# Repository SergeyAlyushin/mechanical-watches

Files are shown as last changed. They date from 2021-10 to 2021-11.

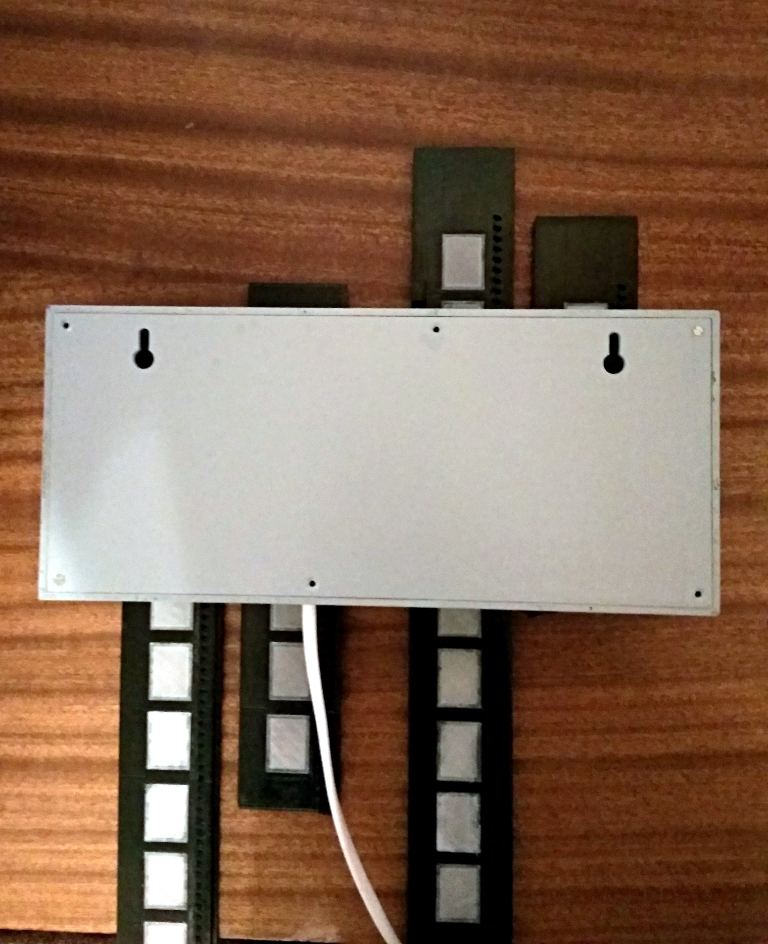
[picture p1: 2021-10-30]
IMG_5.jpg

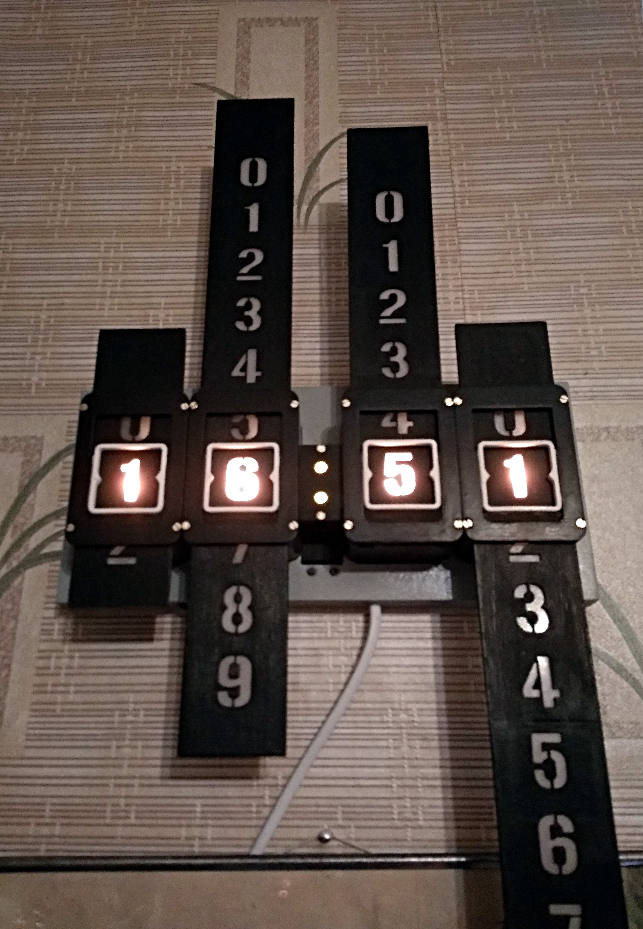
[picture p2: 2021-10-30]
IMG_6.jpg

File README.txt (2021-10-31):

Часы с шаговыми двигателями на Arduino, автор Луук Эссельбрюгге из Нидерландов, напечатанные на 3D-принтере.
Это мой вариант, немного переработанный.
------------------------------------------------------------------------- 

Компоненты:
4 микросхемы SMD 74HC595
4 микросхемы SMD ULN2003  
4 светодиода WS2812B 
1 плата Arduino Nano
1 модуль GPS NEO 6M (покупайте с большой антенной, иначе будете бегать по квартире в поисках спутника)
4 шаговых двигателя 28BYJ-48 на 5V без драйверов
4 резистора SMD 1kOm
2 резистора 0,125Вт 1кОм
1 резистор 0,125Вт 330 Ом
2 светодиода для точек, любого типа, по цвету совпадающие с подсветкой
3 тактовых кнопки DIP
4 концевых выключателя MK7
1 микровыключатель питания
4 разъема ХН2.54 на 5 контактов (папа)
4 разъема ХН2.54 на 4 контакта (папа + мама)
4 разъема ХН2.54 на 3 контакта (папа + мама)
4 разъема ХН2.54 на 2 контакта (папа + мама)
1 блок питания на 5V 3А
16 шурупов 2х10 с полукруглой головкой (для крепления мотора и платы)
24 шурупа 2х10 с головкой в потай (для крепления передних и задних крышек)
12 шурупов 1,8х5 (для крепления модулей)
8 шайб 2х5 (для крепления моторов)
---------------------------------------------------------------------------

Все детали корпуса напечатанны пластиком ABS (его легче склеивать) на 3Д принтере. Четыре корпуса Body 1-4 и корпус Body point печатались с применением поддержек.Файлы STL лежат в папке "Models"
 
4 корпуса (Body_1, Body_2, Body_3, Body_4)
4 крышки корпуса (Bracket)
4 рамки крышки корпуса (Ramka_Bracket)
1 корпус точек (Body_Point)
1 крышка корпуса точек (Lid_Body_point)
1 светофильтр крышки корпуса точек (Filter_point), печать пластиком SBS  
3 пластины (Plate1) 
2 пластины (Plate2)
1 пластина (Plate3)
1 пластина (Plate4)
3 пластинчатых соединителя (Plate_connector)
29 светофильтров пластин (Window), печать пластиком SBS 
4 шестерни шаговых моторов (Gear)
1 половина основания (Top_base_left)
1 половина основания (Top_base_Right)
1 половина задней панели основания (Bottom_base_left)
1 половина задней панели основания (Bottom_base_Right)
1 пластина соединителя задней панели (Pad_Bottom base)
1 крепление антенны GPS (Antenna)
1 крепление модуля GPS (Module GPS)
1 крепление платы Arduino (Arduino)
1 крепление тактовых кнопок (Buttoms)
----------------------------------------------------------------------------
Печатные платы драйверов изготовлены из стеклотекстолита толщиной 1мм, толще не влезут в корпус. Макет платы нарисован в программе Sprint Layout версии 6.0 и лежит в папке "Printed circuit boards".
Принципиальная схема часов лежит в папке "Image".
----------------------------------------------------------------------------
Скетч лежит в папке "ArduinoCode" и полностью работоспособен.
У автора были некоторые неточности, поэтому я внес исправления и позволю себе дать некоторые пояснения для новичков.
В версии Arduino 1.8.1 компиляция проходит без проблем.
-----------------------------------------------------------------------------
Перед загрузкой скетча, проверить, что все ниже перечисленные библиотеки у вас добавлены (они должны быть красного цвета): 
#include <FastLED.h>
#include <SoftwareSerial.h> 
#include <OneWire.h> 
#include <DallasTemperature.h>
Если библиотека черного цвета, то необходимо ее добавить в среду Arduino
-----------------------------------------------------------------------------
В комментариях ниже перечисленных строк:  
int SER_Pin = 12;   //pin 14 on the 75HC595
int RCLK_Pin = 11;  //pin 12 on the 75HC595
int SRCLK_Pin = 10; //pin 11 on the 75HC595
не правильно указана серия микросхемы, правильно - 74НС595
-----------------------------------------------------------------------------
В комментариях строки: 
int RX_GPS = 5; //RX pin on GPS module
не правильно указан контакт подключения модуля GPS, правильно подключать к контакту ТХ.
-----------------------------------------------------------------------------
При необходимости, можно изменить цвет подсветки.
Для дневного режима в строке:
int NightColor[] = {48, 255, 0};
можно поиграться со значениями {48-красный, 255-зеленый, 0-синий}
Для ночного режима в строке:
int DayColor[] = {255, 255, 255};
(этот режим я не использовал, поэтому контакт Arduino А5  я подтянул к GND через резистор 10кОм.)
-----------------------------------------------------------------------------
В зависимости от региона Вашего проживания, возможно будет необходимо подправить значение в строке:
timezoneOffset = 2;
Цифра 2 означает, что к текущему времени GPS будет прибавлено 2 часа.

Для активизации коррекции, вам необходимо нажав и удерживая кнопку "Mode" включить питание часов. Отпустить кнопку только после окончания калибровки.

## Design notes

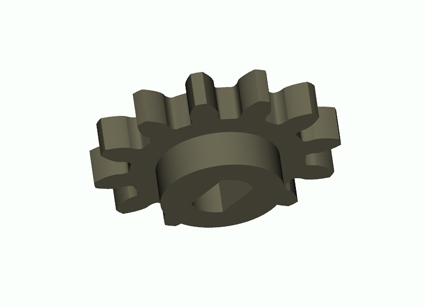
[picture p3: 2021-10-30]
Gear.jpg

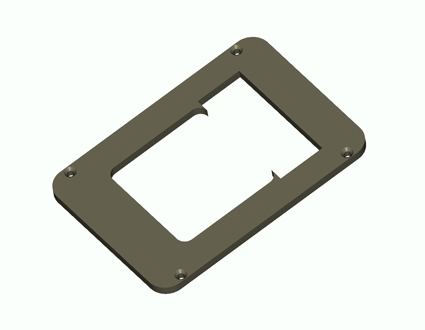
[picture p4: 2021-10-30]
Bracket.jpg

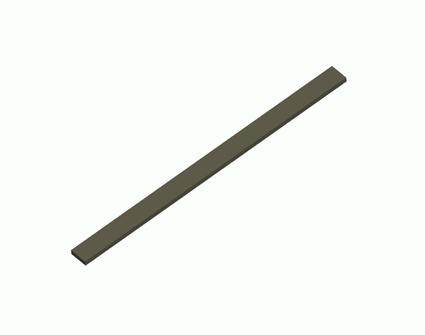
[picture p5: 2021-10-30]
Pad Botton base.jpg

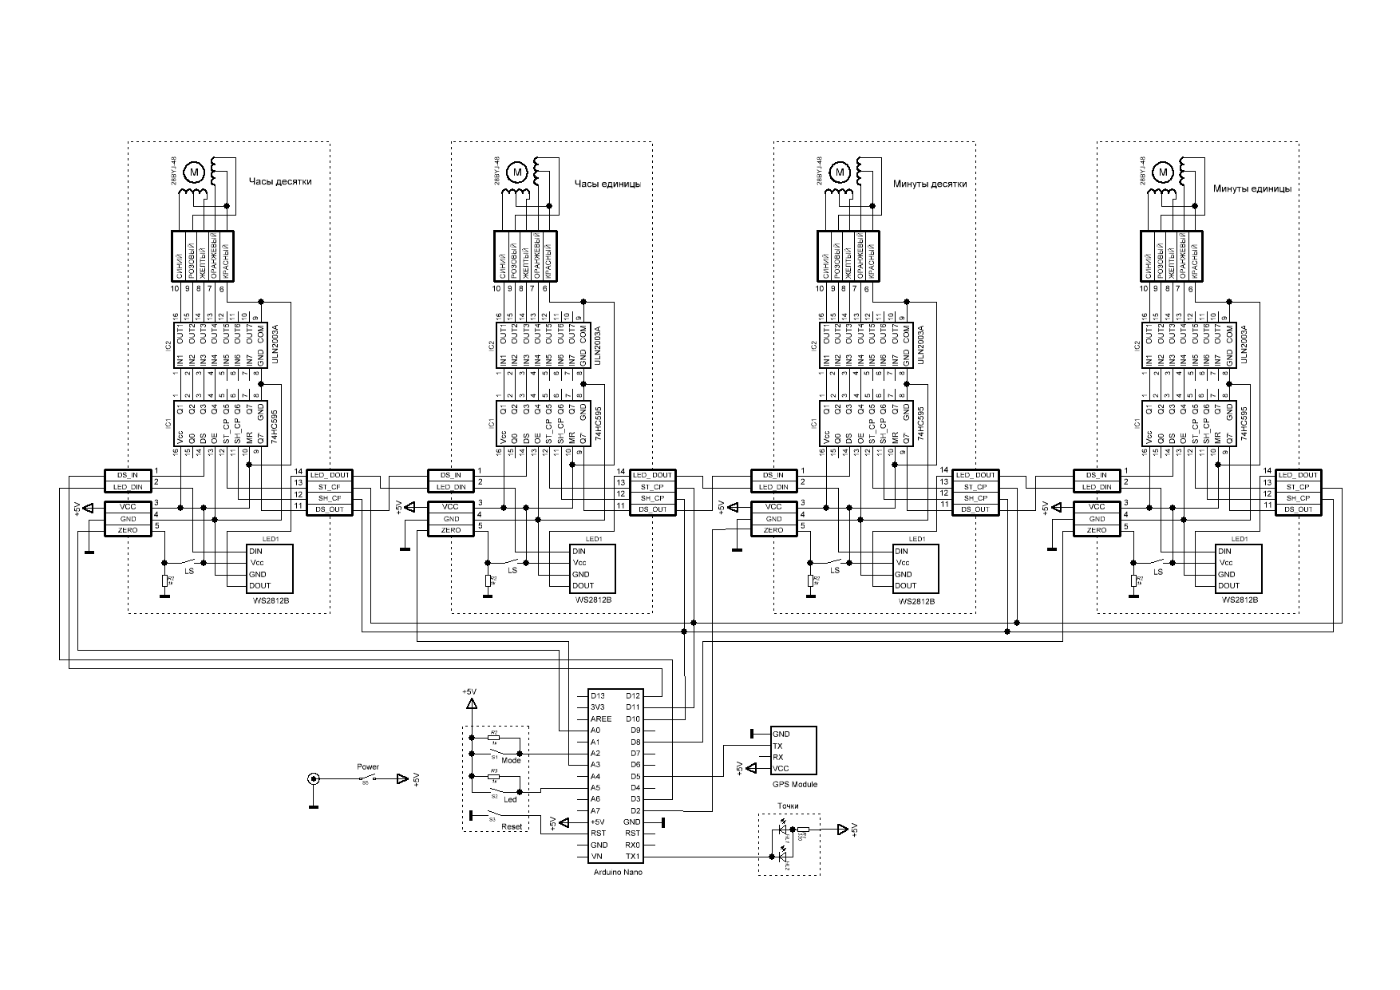
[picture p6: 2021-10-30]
Схема.GIF

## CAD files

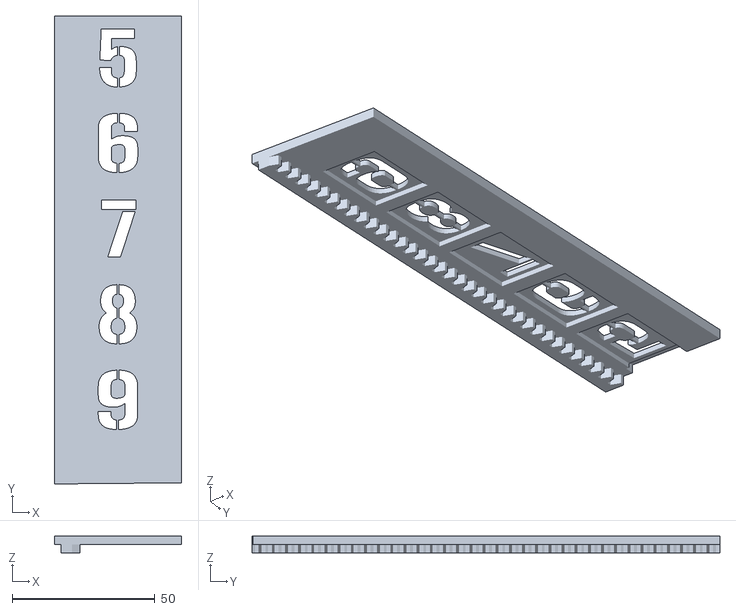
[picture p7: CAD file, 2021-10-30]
Plate2.stl
44.5 x 164.0 x 5.95

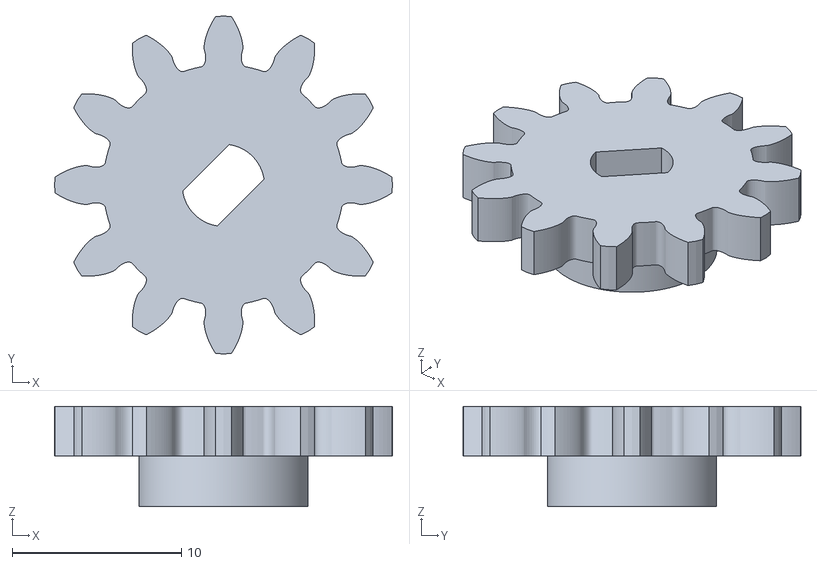
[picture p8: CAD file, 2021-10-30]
Gear.stl
20.0 x 20.0 x 5.93

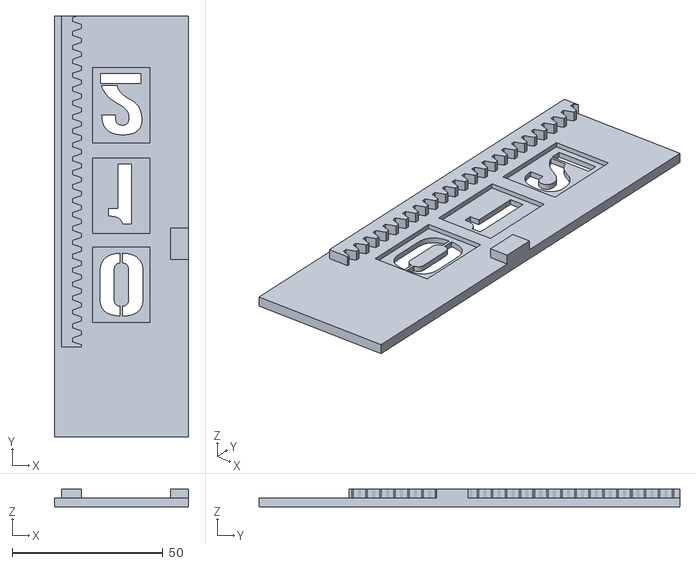
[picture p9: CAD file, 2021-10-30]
Plate3.STL
44.5 x 139.5 x 5.95

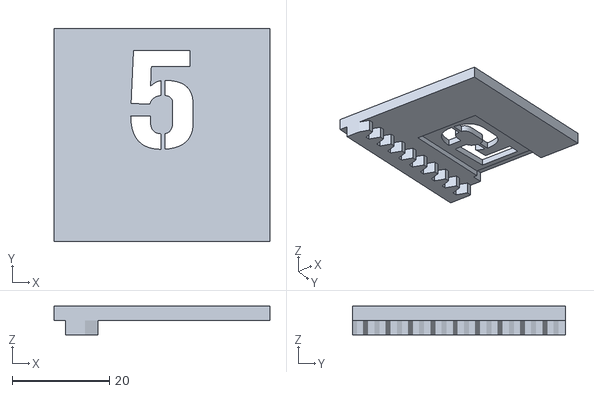
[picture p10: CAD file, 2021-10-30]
Plate4.STL
44.5 x 43.9 x 5.95

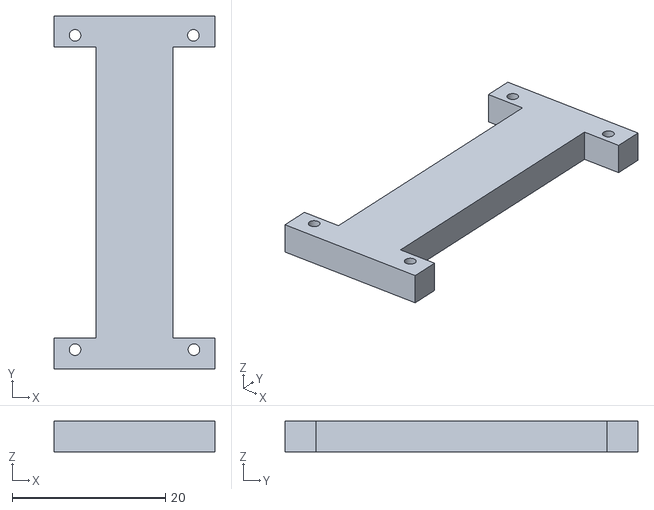
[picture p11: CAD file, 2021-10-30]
Arduino.STL
21.0 x 46.0 x 4.00

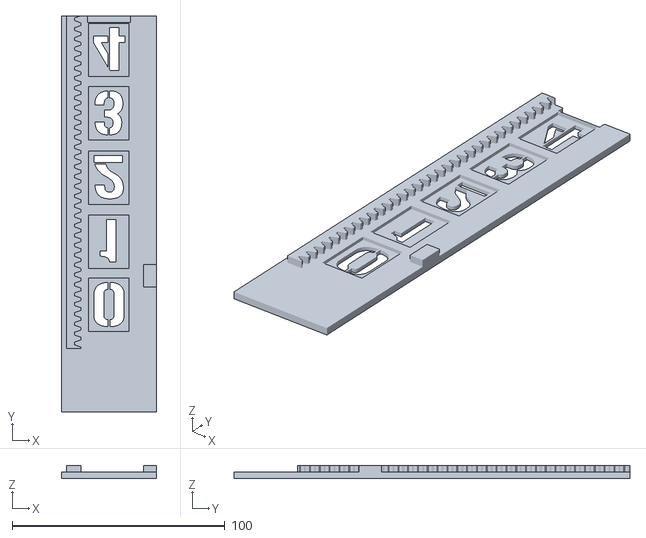
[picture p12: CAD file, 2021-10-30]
Plate1.stl
44.5 x 186.0 x 5.95

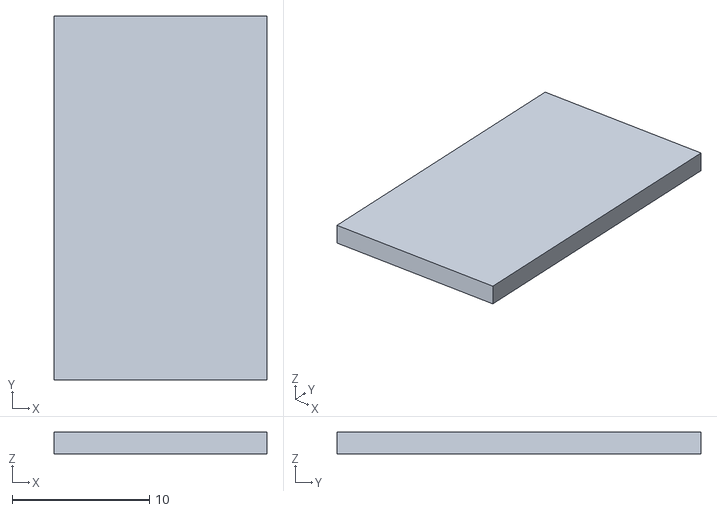
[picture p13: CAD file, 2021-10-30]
Filter point.STL
15.5 x 26.5 x 1.60

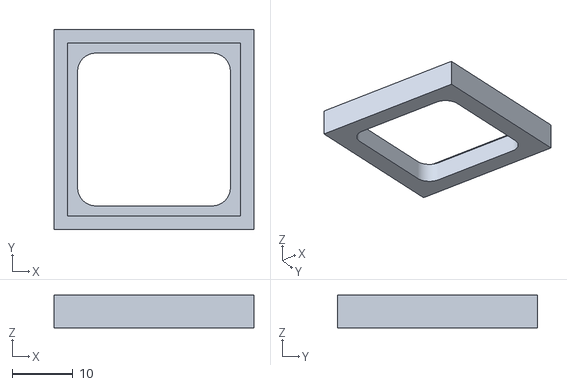
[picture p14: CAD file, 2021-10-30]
Antenna.STL
33.0 x 33.0 x 5.40

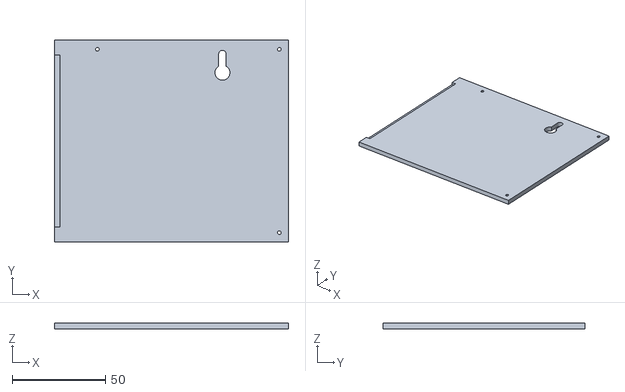
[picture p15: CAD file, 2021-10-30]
Bottom base_Right.STL
125.4 x 108.0 x 3.00

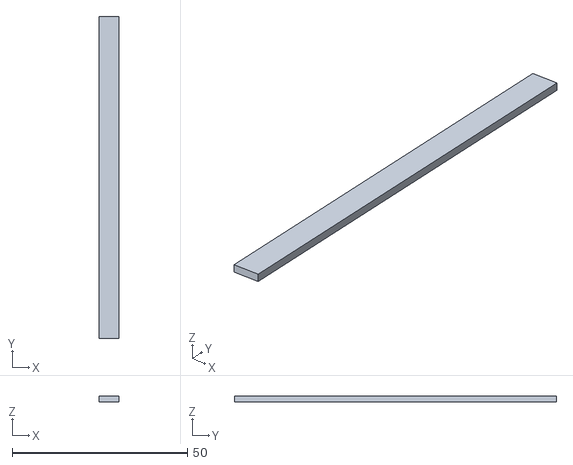
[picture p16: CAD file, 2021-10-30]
Pad Bottom base.STL
5.80 x 91.8 x 1.60

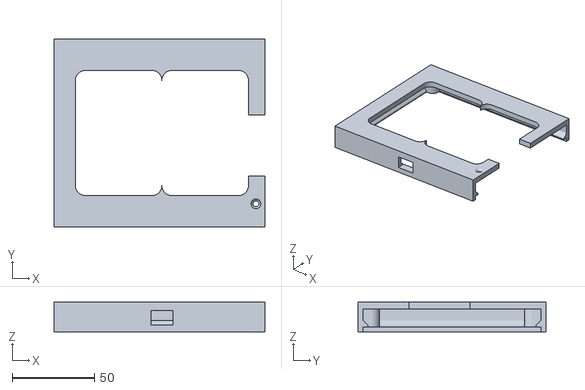
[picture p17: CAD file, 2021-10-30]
Top base_Left.STL
128.5 x 114.2 x 18.0

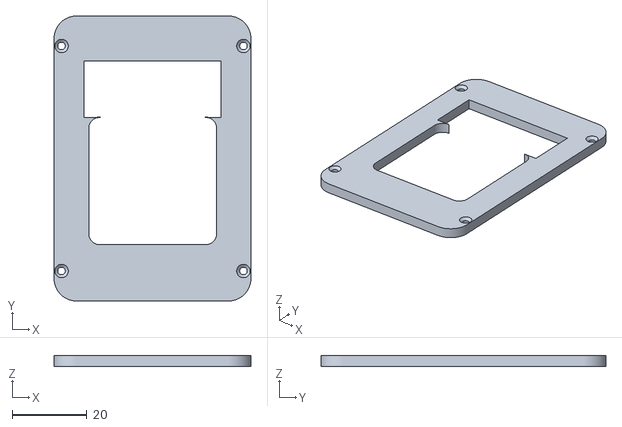
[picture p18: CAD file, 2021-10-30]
Bracket.STL
52.5 x 76.0 x 3.00

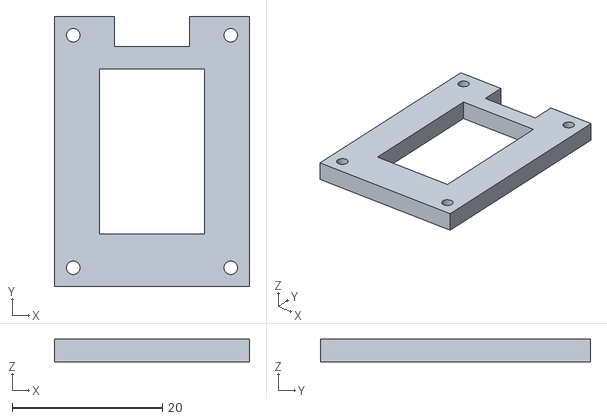
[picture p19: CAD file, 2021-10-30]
Module GPS.STL
26.0 x 36.0 x 3.00

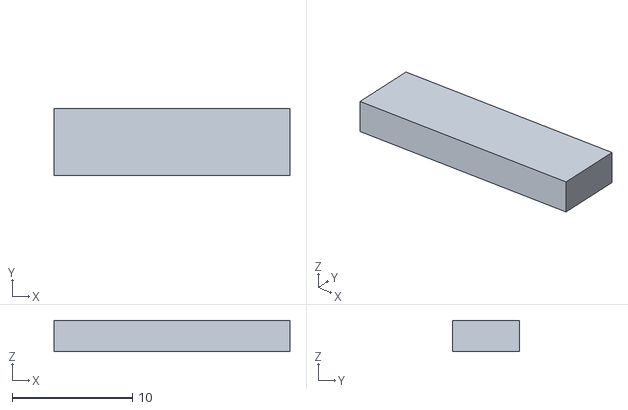
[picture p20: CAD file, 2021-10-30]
PlateConnector.stl
19.6 x 5.60 x 2.60

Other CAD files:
Bottom base_Left.STL
Body_point.STL
Buttons.STL
RamkaBracket.STL
Top base_Right.STL
Window.STL

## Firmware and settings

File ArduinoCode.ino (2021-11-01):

#include <FastLED.h>
#include <SoftwareSerial.h> 
#include <OneWire.h> 
#include <DallasTemperature.h>

int SER_Pin = 12;   //pin 14 on the 74HC595
int RCLK_Pin = 11;  //pin 12 on the 74HC595
int SRCLK_Pin = 10; //pin 11 on the 74HC595

int RX_GPS = 5; //RX pin on GPS module
SoftwareSerial SoftSerial(RX_GPS, 0);

#define LED_TYPE WS2812
#define NUM_LEDS 4
#define DATA_PIN 3
CRGB leds[NUM_LEDS];

OneWire oneWire(6);
DallasTemperature sensors(&oneWire);

#define shiftRegCount 4
#define RegisterPins shiftRegCount * 8
boolean registers[RegisterPins+8];

// Limitswitch Pin, Stepper motor pins shiftregister offset, Calibration offset, CurrentDigit, Amount of Movement left
int MOTORS[4][5] = {
  {A0, 0, 20, 0, 0},
  {A3, 8, 30, 0, 0},
  {2, 16, 30, 0, 0},
  {8, 24, 10, 0, 0}
};

//Switch 1 and 2 pins used for changing color and modes
int SW1 = A5;
int SW2 = A2;

int DayColor[] = {255, 255, 255};
int NightColor[] = {48, 255, 0};

//Clear entire shift register
void clearRegisters(){
  for(int i = RegisterPins - 1; i >=  0; i--){
     registers[i] = LOW;
  }
} 
//Update register
void writeRegisters(){
  digitalWrite(RCLK_Pin, LOW);
  for(int i = RegisterPins - 1; i >=  0; i--){
    digitalWrite(SRCLK_Pin, LOW);
    int val = registers[i];
    digitalWrite(SER_Pin, val);
    digitalWrite(SRCLK_Pin, HIGH);
  }
  digitalWrite(RCLK_Pin, HIGH);
}

//Motor step delay lower then 500 has issues
int motorSpeed = 400;

char currentDate[] = "000000";
char currentTime[] = "000000.00";
//Default offset is CET
int timezoneOffset = 1;

int currentTemp = 0;
int TimeFix = 0;

int ended = 0;
int started = 1;


void setup() {
  FastLED.addLeds<LED_TYPE, DATA_PIN>(leds, NUM_LEDS);
  sensors.begin(); 
  
  Serial.begin(9600);
  
  pinMode(SER_Pin, OUTPUT);
  pinMode(RCLK_Pin, OUTPUT);
  pinMode(SRCLK_Pin, OUTPUT);
  
  for(int x = 0; x < 4; x++){
    pinMode(MOTORS[x][0], INPUT);
  }

  pinMode(SW1, INPUT);
  pinMode(SW2, INPUT);

  //If SW2 pressed on boot change time to UTC +3 (CEST)
  if(digitalRead(SW2)){
    timezoneOffset = 3;
  }

  for(int x = 0; x < 4; x++){
    calibrate(MOTORS[x]);
  }
  clearRegisters();
  writeRegisters();
  Background(1, NightColor);
  SoftSerial.begin(9600);
}

int mode = 1;
int colorMode = 0;
long lastBlink = 0;
int blinkBright = 0;

void loop(){    
   if(digitalRead(SW1)){
    mode = !mode;
   }
   
   if(mode){
    updateDateTime();
    showTime();
   }else{
    updateTemp();
    showTemp();
    BackgroundTemp();
   }
     //Serial.println(currentTime);
}

//Update time when it changes
void showTime(){
  //Stop the serial connection with GPS when driving steppers
  //Because it causes lag
  if(MOTORS[0][4] != 0 || MOTORS[1][4] != 0 || MOTORS[2][4] != 0 || MOTORS[3][4] != 0){
    if(!ended){
      SoftSerial.end();
      ended = 1;
      started = 0;
    }
  }else{
    if(!started){
     SoftSerial.begin(9600);
     started = 1;
     ended = 0;
    }
  }

  //Doing this is ugly but the fast way by substracting -48 from the ASCCI value sometimes caused strange behavior
  //Converting to string first seems to work best
  char tmp[2];
  tmp[1] = 0; 
  for(int x = 0; x < 4; x++){
    tmp[0] = currentTime[x];
    updateDigit2(MOTORS[x], atoi(tmp));
    ///updateDigit(MOTORS[x], atoi(tmp));
  }
}

void showTemp(){
  updateDigit(MOTORS[1], currentTemp / 1000);
  updateDigit(MOTORS[2], currentTemp / 100 % 10);
}

void updateTemp(){
  sensors.requestTemperatures();
  currentTemp = sensors.getTempCByIndex(0) * 100;
}

//Update digit pos type 1; is blocking not used currently
void updateDigit(int motor[], int digit){
  if(motor[3] != digit && digit >= 0 && digit <= 9){
    SoftSerial.end();
    if(digit > motor[3]){
       int x = (digit-motor[3])* (280);
       while(x > 0){
       clockwise(motor[1], motorSpeed);
       x--;
      }
    } else{
      int x = (motor[3]-digit)*(280);
       while(x > 0){
       counterclockwise(motor[1], motorSpeed);
       x--;
      }
    }
    SoftSerial.begin(9600);
    motor[3] = digit;
    clearstepper(motor[1]);
  }

}

//Update digit type 2; is non blocking
void updateDigit2(int motor[], int digit){
  if(motor[3] != digit && digit >= 0 && digit <= 9){
    if(digit > motor[3]){
       if(motor[4] == 0){
        motor[4] = (digit-motor[3])* (280);
       }
       clockwise(motor[1], motorSpeed);
       motor[4]--;  
      }
      else{
       if(motor[4] == 0){
        motor[4] = (motor[3]-digit)*(280);
       }
       counterclockwise(motor[1], motorSpeed);
       motor[4]--; 
      }
      
      if(motor[4] == 0){
       motor[3] = digit;
       clearstepper(motor[1]);
      }
    } 
  }

//Move motor back to zero
void calibrate(int motor[]){
  while(!digitalRead(motor[0])){
     counterclockwise(motor[1], 500);
  }
  //calibration offset
  for(int x = 0; x <= motor[2]; x++){
     clockwise(motor[1], 500);
  }
  motor[3] = 0;
  clearRegisters();
  writeRegisters();
}

//Very nice and cool compact code for reading GPS time
char tmpTime[] = "000000.00";
//GPS time header
char header[] = "$GPRMC";
int charCount = 0;
int match = 0;
int item = 0;
int itemCount = 0;
int timeReady = 0;
void updateDateTime(){
  while (SoftSerial.available() > 0) {
      char c = SoftSerial.read();
      Serial.write(c);
      if(match){
          if(c >= 48 && c <= 57 || c == 46){
           tmpTime[itemCount] = c;
           itemCount++;
          }
        if(c == ','){
          if(currentTime != tmpTime && itemCount == 9){
            //Add timezone offset
            memcpy(currentTime, tmpTime, 8);
            int A = int(currentTime[0])-48;
            int B = int(currentTime[1])-48;
            
            int hour = A*10+(B+timezoneOffset);
            if(hour > 23){
              hour -= 24;
            }
            currentTime[0] = 48 + hour / 10;
            currentTime[1] = 48 + hour % 10;
            Serial.println(currentTime);
          }
          itemCount = 0;
          match = 0;
          item = 0;
        }
      }else{
        if(charCount >= 6){
          charCount = 0;
          match = 1;
        }
        if (header[charCount] == c){
           charCount++;
        }else{
           charCount = 0;
        }
      }
}
}

void Background(int br, int color[]){
  leds[0] = CRGB(color[0], color[1], color[2]);
  leds[1] = CRGB(color[0], color[1], color[2]);
  leds[2] = CRGB(color[0], color[1], color[2]);
  leds[3] = CRGB(color[0], color[1], color[2]);
  if(br){
    FastLED.setBrightness(255);
  }else{
    FastLED.setBrightness(200);
  }
  
    FastLED.show();
    FastLED.show();
}

void BackgroundTemp(){
  if(currentTemp < 15){
    leds[1] = CRGB(0, 0, 255);
    leds[2] = CRGB(0, 0, 255);
  }
  if(currentTemp > 20 && currentTemp < 25){
    leds[1] = CRGB(0, 255, 0);
    leds[2] = CRGB(0, 255, 0);
  }
  if(currentTemp > 25){
    leds[1] = CRGB(255, 0, 0);
    leds[2] = CRGB(255, 0, 0);
  }
  
  leds[0] = CRGB(0, 0, 0);
  leds[3] = CRGB(0, 0, 0);
  FastLED.show();
}

void setRegisterPin(int index, int value){
  registers[index] = value;
}

void clearstepper(int offset){
  setRegisterPin(1+offset, LOW);
  setRegisterPin(2+offset, LOW);
  setRegisterPin(3+offset, LOW);
  setRegisterPin(4+offset, LOW);
  writeRegisters(); 
}

void counterclockwise (int offset, int motorSpeed){
  // 1
  setRegisterPin(1+offset, HIGH);
  setRegisterPin(2+offset, LOW);
  setRegisterPin(3+offset, LOW);
  setRegisterPin(4+offset, LOW);
  writeRegisters(); 
  delayMicroseconds(motorSpeed);
  // 2
  setRegisterPin(1+offset, HIGH);
  setRegisterPin(2+offset, HIGH);
  setRegisterPin(3+offset, LOW);
  setRegisterPin(4+offset, LOW);
  writeRegisters(); 
  delayMicroseconds (motorSpeed);
  // 3
  setRegisterPin(1+offset, LOW);
  setRegisterPin(2+offset, HIGH);
  setRegisterPin(3+offset, LOW);
  setRegisterPin(4+offset, LOW);
  writeRegisters(); 
  delayMicroseconds(motorSpeed);
  // 4
  setRegisterPin(1+offset, LOW);
  setRegisterPin(2+offset, HIGH);
  setRegisterPin(3+offset, HIGH);
  setRegisterPin(4+offset, LOW);
  writeRegisters(); 
  delayMicroseconds(motorSpeed);
  // 5
  setRegisterPin(1+offset, LOW);
  setRegisterPin(2+offset, LOW);
  setRegisterPin(3+offset, HIGH);
  setRegisterPin(4+offset, LOW);
  writeRegisters(); 
  delayMicroseconds(motorSpeed);
  // 6
  setRegisterPin(1+offset, LOW);
  setRegisterPin(2+offset, LOW);
  setRegisterPin(3+offset, HIGH);
  setRegisterPin(4+offset, HIGH);
  writeRegisters(); 
  delayMicroseconds (motorSpeed);
  // 7
  setRegisterPin(1+offset, LOW);
  setRegisterPin(2+offset, LOW);
  setRegisterPin(3+offset, LOW);
  setRegisterPin(4+offset, HIGH);
  writeRegisters(); 
  delayMicroseconds(motorSpeed);
  // 8
  setRegisterPin(1+offset, HIGH);
  setRegisterPin(2+offset, LOW);
  setRegisterPin(3+offset, LOW);
  setRegisterPin(4+offset, HIGH);
  writeRegisters(); 
  delayMicroseconds(motorSpeed);
}

void clockwise(int offset, int motorSpeed){
  // 1
  setRegisterPin(4+offset, HIGH);
  setRegisterPin(3+offset, LOW);
  setRegisterPin(2+offset, LOW);
  setRegisterPin(1+offset, LOW);
  writeRegisters(); 
  delayMicroseconds(motorSpeed);
  // 2
  setRegisterPin(4+offset, HIGH);
  setRegisterPin(3+offset, HIGH);
  setRegisterPin(2+offset, LOW);
  setRegisterPin(1+offset, LOW);
  writeRegisters(); 
  delayMicroseconds (motorSpeed);
  // 3
  setRegisterPin(4+offset, LOW);
  setRegisterPin(3+offset, HIGH);
  setRegisterPin(2+offset, LOW);
  setRegisterPin(1+offset, LOW);
  writeRegisters(); 
  delayMicroseconds(motorSpeed);
  // 4
  setRegisterPin(4+offset, LOW);
  setRegisterPin(3+offset, HIGH);
  setRegisterPin(2+offset, HIGH);
  setRegisterPin(1+offset, LOW);
  writeRegisters(); 
  delayMicroseconds(motorSpeed);
  // 5
  setRegisterPin(4+offset, LOW);
  setRegisterPin(3+offset, LOW);
  setRegisterPin(2+offset, HIGH);
  setRegisterPin(1+offset, LOW);
  writeRegisters(); 
  delayMicroseconds(motorSpeed);
  // 6
  setRegisterPin(4+offset, LOW);
  setRegisterPin(3+offset, LOW);
  setRegisterPin(2+offset, HIGH);
  setRegisterPin(1+offset, HIGH);
  writeRegisters(); 
  delayMicroseconds (motorSpeed);
  // 7
  setRegisterPin(4+offset, LOW);
  setRegisterPin(3+offset, LOW);
  setRegisterPin(2+offset, LOW);
  setRegisterPin(1+offset, HIGH);
  writeRegisters(); 
  delayMicroseconds(motorSpeed);
  // 8
  setRegisterPin(4+offset, HIGH);
  setRegisterPin(3+offset, LOW);
  setRegisterPin(2+offset, LOW);
  setRegisterPin(1+offset, HIGH);
  writeRegisters(); 
  delayMicroseconds(motorSpeed);
}

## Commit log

2021-10-31 Printed circuit boards
2021-10-31 Create ArduinoCode
